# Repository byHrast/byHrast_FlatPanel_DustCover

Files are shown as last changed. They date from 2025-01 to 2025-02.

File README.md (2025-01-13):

I HAVE SOME SMALL BUGS TO HANDLE AND FUNCTIONALITIES TO ADD. 

ASCOM driver Project for the CoverCalibrator (Flat Panel and Dust Cover)

open


I've developed a universal PCB board, which I plan to use in some of my other projects. 
You can see the EasyEDA project in the dedicated folder. 
board

Also, there is a 3D model for the projects. It fits SW ED120/900. You can find it in the folder.

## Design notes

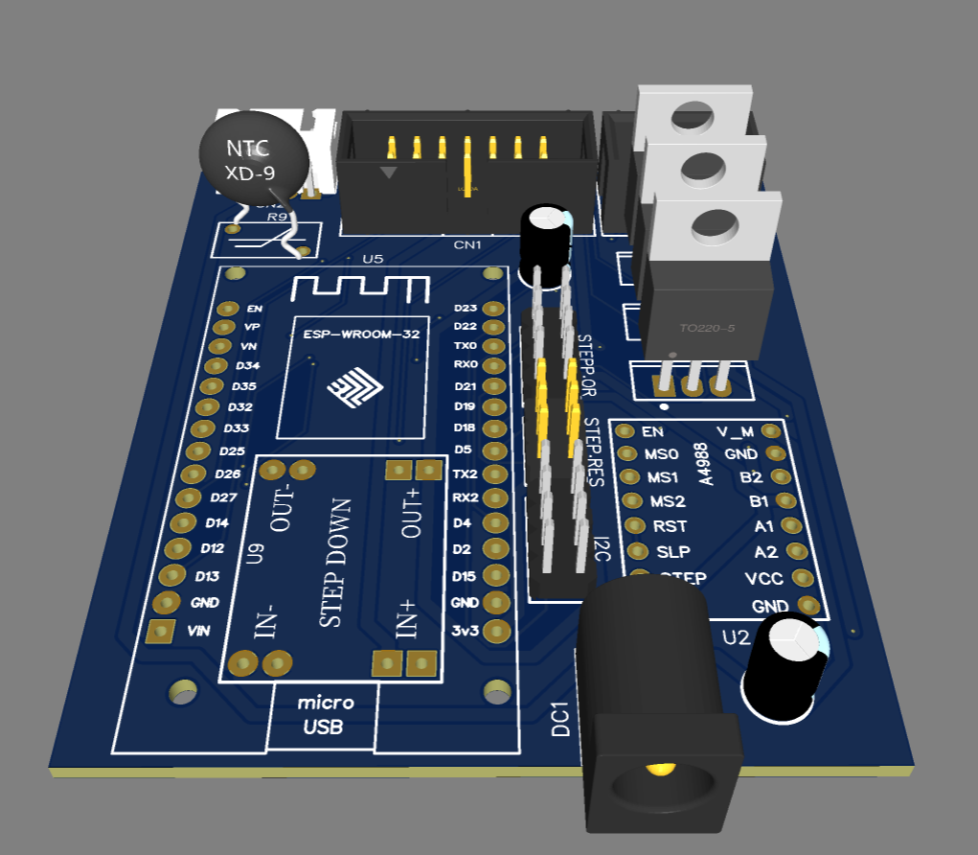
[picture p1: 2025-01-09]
EasyEDA project/board.PNG

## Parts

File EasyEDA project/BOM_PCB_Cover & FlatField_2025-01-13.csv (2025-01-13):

ID | Name | Designator | Footprint | Quantity | Manufacturer Part | Manufacturer | Supplier | Supplier Part | Price
1 | DS254P-2X3-L0 | CN3 | IDC-TH_6P-P2.54-V-R2-C3-S2.54 | 1
2 | 210S-2*4P L=11.6MMGold-plated black | STEPP.OR,I2C | HDR-TH_8P-P2.54-V-M-R2-C4-S2.54 | 2
3 | 100uF | C1,C2 | CAP-TH_BD5.0-P2.00-D0.8-FD | 2
4 | DS254P-2X7-L0 | CN1 | IDC-TH_14P-P2.54-V-R2-C7-S2.54 | 1
5 | XH-4AW_C722872 | CN2 | CONN-TH_XH-4AW_C722872 | 1
6 | DC-005B-2.5A-2.0 | DC1 | DC-IN-TH_DC-005-20A | 1
7 | IRLB8721PBF | Q1,Q2,Q3 | TO-220-3_L10.0-W4.5-P2.54-L | 3
8 | NTC | R9 | RES-TH_L10.5-W5.5-P7.50-D0.6-S5.50 | 1
9 | A4988 Driver | U2 | DRIVER A4988 | 1
10 | STEP DOWN | U9 | STEP DOWN | 1
11 | 210-72-03GB01 | STEP.RES | HDR-TH_6P-P2.54-V-R2-C3-S2.54_A2541WV-2X3P | 1
12 | ESP32 | U5 | ESP32 DEVELOPMENT KIT | 1
13 | 200 | R1,R3,R5 | R1206 | 3
14 | 10K | R2,R4,R6,R7,R8 | R1206 | 5

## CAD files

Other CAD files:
3d model/FlatfieldV3 v10.f3z

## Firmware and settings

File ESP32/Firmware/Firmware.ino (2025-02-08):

#include "WiFi.h"
#include "ESPAsyncWebServer.h" // Use ESP32_Async_Web_Server library  https://github.com/byHrast/byHrast_FlatPanel_DustCover/tree/main/ESP32
#include "SPIFFS.h"
#include "ESP32Servo.h"
#include "ESPmDNS.h"
ESP32PWM pwm;

// Defaultne WiFi postavke
const char* ssid     = "FlatPanel";
const char* password = "123456789";
IPAddress local_IP(192, 168, 1, 112);
IPAddress gateway(192, 168, 1, 1);
IPAddress subnet(255, 255, 255, 0);
IPAddress primaryDNS(8, 8, 8, 8);   //optional
IPAddress secondaryDNS(8, 8, 4, 4); //optional
const char* hostname = "FlatPanelByHrast";

//Servo varijable
Servo myservo;  // create servo object to control a servo
// Recommended PWM GPIO pins on the ESP32 include 2,4,12-19,21-23,25-27,32-33
int servoPin = 13;
int servoENA = 32;

// Definiranje IO
const int ledPWM = 0;
const int ledENA = 26;
int ledMax = 100;
const int heaterENA = 27;

int thermistorPin1 = 25;   // Thermistor u panelu
int thermistorValue1 = 0;
int thermistorPin2 = 15;   // Thermistor na plocici
int thermistorValue2 = 0;

//Pomocne varijable
String ledState = "OFF";
String heaterState = "OFF";
String coverState = "CLOSED";
int pos = 180;  // variable to store the servo position

// Timer bez delay-a varijable
unsigned long previousMillis = 0;  // will store last time LED was updated
const long interval = 1000;  // interval at which to blink (milliseconds)

// Create AsyncWebServer object on port 80
AsyncWebServer server(80);

// Ova fja obrađuje u html-u varijable omeđene s % i generira vrijednosti
String processor(const String& var) {
  // Return LED state
  if (var == "STATE") return ledState;

  // Determine cover state based on position
  if (var == "STATE2") return (pos >= 180) ? "CLOSED" : (pos <= 0) ? "OPEN" : "MOVING";

  // Return heater state based on heaterENA pin state
  if (var == "STATE3") return digitalRead(heaterENA) ? "ON" : "OFF";

  // Retrieve Wi-Fi settings from SPIFFS
  if (var == "SSID") return getValue(spiffsRead("WL"), ';', 0);
  if (var == "PASS") return getValue(spiffsRead("WL"), ';', 1);
  //if (var == "iP") return getValue(spiffsRead("WL"), ';', 2);
  if (var == "iP") return WiFi.localIP().toString();

  // Default return if no match
  return String();
}



void setup() {
  // Serial port for debugging purposes
  Serial.begin(115200);

  ESP32PWM::allocateTimer(0);
  ESP32PWM::allocateTimer(1);
  ESP32PWM::allocateTimer(2);
  ESP32PWM::allocateTimer(3);
  myservo.attach(servoPin, 500, 2400);  // attaches the servo on pin 18 to the servo object

  pinMode(servoENA, OUTPUT);
  pinMode(ledENA, OUTPUT);
  pinMode(heaterENA, OUTPUT);

  // Initialize SPIFFS
  if (!SPIFFS.begin(true)) {
    //Serial.println("An Error has occurred while mounting SPIFFS");
    return;
  }

  initWiFi();

  server.on("/", HTTP_GET, handleRootRequest);
  server.on("/style.css", HTTP_GET, [](AsyncWebServerRequest * request) {
    request->send(SPIFFS, "/style.css", "text/css");
  });
  server.on("/jquery.min.js", HTTP_GET, [](AsyncWebServerRequest * request) {
    request->send(SPIFFS, "/jquery.min.js", "text/css");
  });
  server.on("/LEDstatus.htm", HTTP_GET, handleLEDStatus);
  server.on("/HEATERstatus.htm", HTTP_GET, handleHeaterStatus);
  server.on("/COVERstatus.htm", HTTP_GET, handleCoverStatus);

  server.begin();
}

void loop() {
  processSerialCommand();
}

String getValue(String data, char separator, int index) ///////// fja koja  dijeli veliki string na segmente stringova odvojene separatorom, npr., zerez ili točka zarez
{
  int found = 0;
  int strIndex[] = { 0, -1 };
  int maxIndex = data.length() - 1;

  for (int i = 0; i <= maxIndex && found <= index; i++) {
    if (data.charAt(i) == separator || i == maxIndex) {
      found++;
      strIndex[0] = strIndex[1] + 1;
      strIndex[1] = (i == maxIndex) ? i + 1 : i;
    }
  }
  return found > index ? data.substring(strIndex[0], strIndex[1]) : "";
}

char* string2char(String command) { //// fja koja dijeli string u char
  if (command.length() != 0) {
    char *p = const_cast<char*>(command.c_str());
    return p;
  }
}


String spiffsRead (String FileName) { /// citanje spiffs datoteka
  File file = SPIFFS.open("/" + FileName + ".txt", FILE_READ);
  String Sval;
  if (!file) {
    ////Serial.println("Failed to open file for reading");
  }
  while (file.available()) {
    Sval = file.readString(); /////////////////pročitana datoteka će biti spremljena u varijablu Sval i fja vraća tu varijablu
    //////Serial.println("Učitavam : " + FileName + " : " + Sval);
  }
  file.close();
  return Sval;
}

String spiffsWrite (String filename, String podaci) { ////fja koja zapisuje podatke u odgovarajucu txt datoteku
  File file = SPIFFS.open("/" + filename + ".txt", FILE_WRITE);

  if (!file) {
    ////Serial.println("There was an error opening the file for writing");
  }
  if (file.print(podaci)) {

  } else {
    ////Serial.println("File write failed");
  }
  file.close();
  return String();
}

void closeCover() {
  //digitalWrite(servoENA, LOW);
  myservo.attach(servoPin, 500, 2400);
  if (coverState != "CLOSED") {
    for (pos = 0; pos <= 180; pos++) {  // goes from 0 degrees to 180 degrees
      // in steps of 1 degree
      myservo.write(pos);  // tell servo to go to position in variable 'pos'
      delay(15);           // waits 15ms for the servo to reach the position
    }
    Serial.print("#");
    //  digitalWrite(servoENA, HIGH);

  }
  coverState = "CLOSED";
  analogWriteFrequency(ledENA, 1000);
  myservo.detach();
}

void openCover() {
  myservo.attach(servoPin, 400, 2500);
  // digitalWrite(servoENA, LOW);
  if (coverState != "OPEN") {
    for (pos = 180; pos >= 0; pos--) {  // goes from 180 degrees to 0 degrees
      myservo.write(pos);                  // tell servo to go to position in variable 'pos'
      delay(15);                           // waits 15ms for the servo to reach the position
    }
    Serial.print("#");
    // digitalWrite(servoENA, HIGH);
  }
  coverState = "OPEN";
  analogWriteFrequency(ledENA, 1000);
  myservo.detach();
}

void ledON (int P) {
  /// Reset freq change coused by ServoESP32 library
  analogWrite(ledENA, P);
  if (P == 0) ledState = "OFF";
  else ledState = "ON";
}

void initWiFi() {
  Serial.println("Initializing WiFi...");

  String val = spiffsRead("WL");
  String ssid = getValue(val, ';', 0);
  String pass = getValue(val, ';', 1);

  Serial.println("SSID: " + ssid + "  PASS: " + pass);

  WiFi.setHostname(hostname);
  WiFi.mode(WIFI_STA);
  WiFi.begin(ssid.c_str(), pass.c_str());

  int attempts = 0;
  while (WiFi.status() != WL_CONNECTED && attempts < 10) {
    delay(1000);
    Serial.print(".");
    attempts++;
  }

  if (WiFi.status() == WL_CONNECTED) {
    Serial.println("\nConnected to WiFi!");
    Serial.println("IP Address: " + WiFi.localIP().toString());
  } else {
    Serial.println("\nWiFi connection failed. Starting AP mode...");

    if (!WiFi.config(local_IP, gateway, subnet, primaryDNS, secondaryDNS)) {
      Serial.println("STA Failed to configure");
    }

    WiFi.mode(WIFI_AP);
    WiFi.softAP(ssid.c_str(), pass.c_str());

    Serial.print("AP IP address: ");
    Serial.println(WiFi.softAPIP());
  }

    if (!MDNS.begin("FlatPanel")) {
        Serial.println("Error setting up MDNS!");
        return;
    }
    Serial.println("mDNS responder started");
  
}

void processSerialCommand() {
  if (!Serial.available()) return; // Exit if no data available

  String cmd = Serial.readStringUntil('#');
  cmd.trim(); // Remove any leading/trailing whitespace

  if (cmd == "heaterON") {
    digitalWrite(heaterENA, HIGH);
  } else if (cmd == "heaterOFF") {
    digitalWrite(heaterENA, LOW);
  } else if (cmd == "50") {
    // analogWrite(ledENA, 127);
  } else if (cmd == "100") {
    // analogWrite(ledENA, 256);
  } else if (cmd == "close") {
    closeCover();
  } else if (cmd == "open") {
    openCover();
  }
}

void handleRootRequest(AsyncWebServerRequest *request) {
  request->send(SPIFFS, "/index.html", String(), false, processor);

  int paramsNr = request->params();
  String ssid, pass;
  bool writeToSPIFFS = false;

  for (int i = 0; i < paramsNr; i++) {
    const AsyncWebParameter* p = request->getParam(i);
    String name = p->name();
    String value = p->value();

    if (name == "led") {
      ledON(value.toInt() ? ledMax : 0);
    } else if (name == "heater") {
      digitalWrite(heaterENA, value.toInt() ? HIGH : LOW);
    } else if (name == "cover") {
      value.toInt() ? openCover() : closeCover();
    } else if (name == "SSID") {
      ssid = value;
    } else if (name == "PASS") {
      pass = value;
      writeToSPIFFS = true;
    }
  }

  if (writeToSPIFFS) {
    spiffsWrite("WL", ssid + ";" + pass);
  }
}

void handleLEDStatus(AsyncWebServerRequest *request) {
  request->send(SPIFFS, "/LEDstatus.htm", String(), false, processor);

  if (request->hasParam("led")) {
    String value = request->getParam("led")->value();
    ledON(value.toInt());
    ledState = value;
  }
}

void handleHeaterStatus(AsyncWebServerRequest *request) {
  request->send(SPIFFS, "/HEATERstatus.htm", String(), false, processor);

  if (request->hasParam("heater")) {
    digitalWrite(heaterENA, request->getParam("heater")->value().toInt() ? HIGH : LOW);
  }
}

void handleCoverStatus(AsyncWebServerRequest *request) {
  request->send(SPIFFS, "/COVERstatus.htm", String(), false, processor);

  if (request->hasParam("cover")) {
    request->getParam("cover")->value().toInt() ? openCover() : closeCover();
  }
}

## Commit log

2025-02-06 Add files via upload
    Some BUG fixes;
    1) ServoESP32 libary uses PPM so it messes up PWM of ledENA, so I added; analogWriteFrequency(ledENA, 1000);
    2) Changed the way to read a state of the ledENA from digitalRead to analogRead (as the ledENA is PWM)
    [Firmware.ino]
2025-02-06 Delete ESP32/Firmware - Copy.ino
    This was a backup file to the project. So, not needed.
2025-02-06 Add files via upload
    Some bug fixes and additional features.
    Now you can set values from 0 to 255 for the PWM output.
    [Firmware.ino]
2025-02-06 Delete ESP32/Firmware/FlatPanel directory
    Early version so I deleted the folder.
2025-02-06 Add files via upload
    Some fixes and added functionality. Now it's possible to set LED brightness from 0 to 255.
2025-02-08 Add files via upload
    Added ESPmDNS.h so you can open web interface via http://flatpanel.local
    Small bugfixes.
    [Firmware.ino]
